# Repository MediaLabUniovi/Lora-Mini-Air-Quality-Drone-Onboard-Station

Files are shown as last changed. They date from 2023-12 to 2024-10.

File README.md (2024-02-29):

<div align="right">

spanish | english

</div>



<div align="center">

# MINI ESTACIÓN DE CALIDAD DEL AIRE CONECTADA POR LORA A BORDO DE UN DRONE

 [![Build with PlatformIO](https://img.shields.io/badge/build%20with-PlatformIO-orange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)](https://platformio.org/)

## Proyecto basado en: [alexcorvis84/mini-lora-weatherstation](https://github.com/alexcorvis84/mini-lora-weatherstation)

</div>

___

<div align="justify">

## Índice
- [Introducción](https://github.com/medialablpwan/droneloraminiairqualitystation/blob/main/README.md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)
- [Características principales](https://github.com/medialablpwan/droneloraminiairqualitystation/blob/main/README.md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)
- [Lista de componentes](https://github.com/medialablpwan/droneloraminiairqualitystation/blob/main/README.md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)
- [Lista de conexiones](https://github.com/medialablpwan/droneloraminiairqualitystation/blob/main/README.md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)
- [Flujograma (¡Simplificado!)](https://github.com/medialablpwan/droneloraminiairqualitystation/blob/main/README.md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)
- [Archivos de código](https://github.com/medialablpwan/droneloraminiairqualitystation/blob/main/README.md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)
- [Ejemplos consultados](https://github.com/medialablpwan/loraminiairqualitydroneonboardstation/blob/main/README.md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)
- [Experimento de implementación](https://github.com/medialablpwan/droneloraminiairqualitystation/blob/main/README.md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)
- [Licencia](https://github.com/medialablpwan/droneloraminiairqualitystation/blob/main/README.md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)
- [Contacto](https://github.com/medialablpwan/droneloraminiairqualitystation/blob/main/README.md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)

</div>

___

<div align="justify">

## Introducción [:leftwards_arrow_with_hook:](https://github.com/medialablpwan/droneloraminiairqualitystation/blob/main/README.md#%C3%ADndice)

Como parte de mi Trabajo de Fin de Grado sobre drones y sensorización, en Medialab_ LPWAN, se me dio a conocer la tecnología de LoRaWAN. Con ella, entendí rápidamente el potencial de trabajar en un sensor de calidad de aire que montar en un drone de _long range_ para ser usado como plataforma móvil y medir a kilómetros de distancia atmósferas hostiles en caso de accidente donde fuese peligroso enviar a un equipo de personas. Como resultado, nació el sensor _on-board_ que os voy a mostrar como un nodo conectado por LoRa, sincronizable con [The Things Network](https://www.thethingsnetwork.org/), que montarle al drone que construí sin que la cobertura fuese un factor limitante.

</div>

<div align="center">
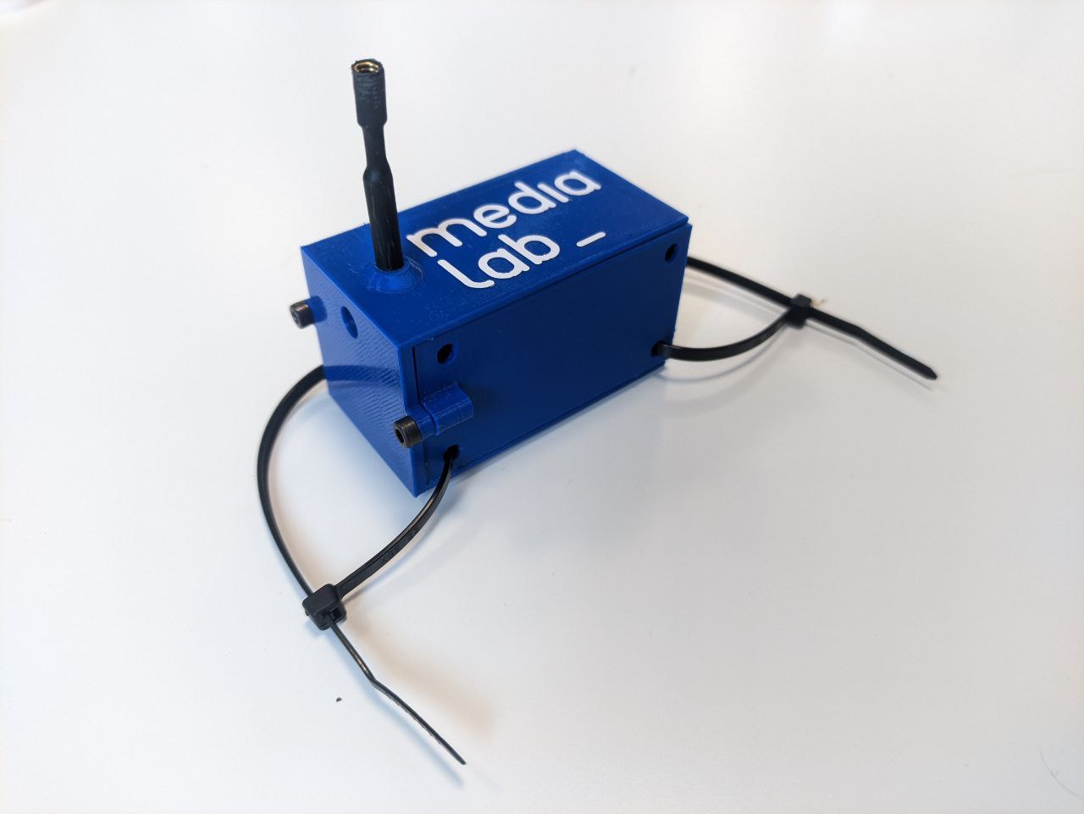
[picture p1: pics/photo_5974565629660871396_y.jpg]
  
</div>
<br/>

<p align="justify"> En este repositorio, encontrarás todos los archivos y guías educativas necesarias para entender con totalidad e incluso tomarte la libertad creativa de mejorar este proyecto. Las carpetas y archivos han sido llamados con nombres que se explican a ellos mismos para hacer la navegación más intuitiva. </p>

___

### <p align="justify"> Características principales [:leftwards_arrow_with_hook:](https://github.com/medialablpwan/droneloraminiairqualitystation/blob/main/README.md#%C3%ADndice) </p>

- <p align="justify"> Desarrollado usando la HelTec CubeCell HTCC-AB01 (Una placa de muy bajo consumo con LoRa implementado y que soporta recarga con panel solar y gestión de batería) </p>

  <div align="center">
    
  </div>
  <br/>

- <p align="justify"> Cambios realizados para añadirle, además, un sensor CCS811 (Sensor de partículas volátiles) </p>

  <div align="center">
    
  </div>
  <br/>

- <p align="justify"> Carcasa a medida para encapsular todos los componentes a un tamaño similar al de la batería del drone (Envase + Recipiente) </p>

  <div align="center">
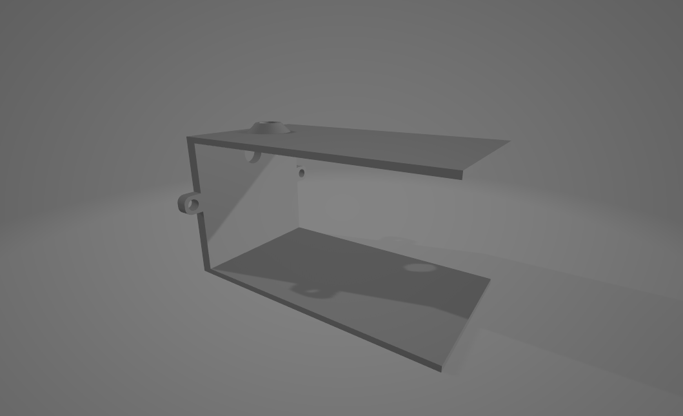
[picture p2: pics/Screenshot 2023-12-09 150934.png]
    
  </div>
  <br/>
  <div align="center">
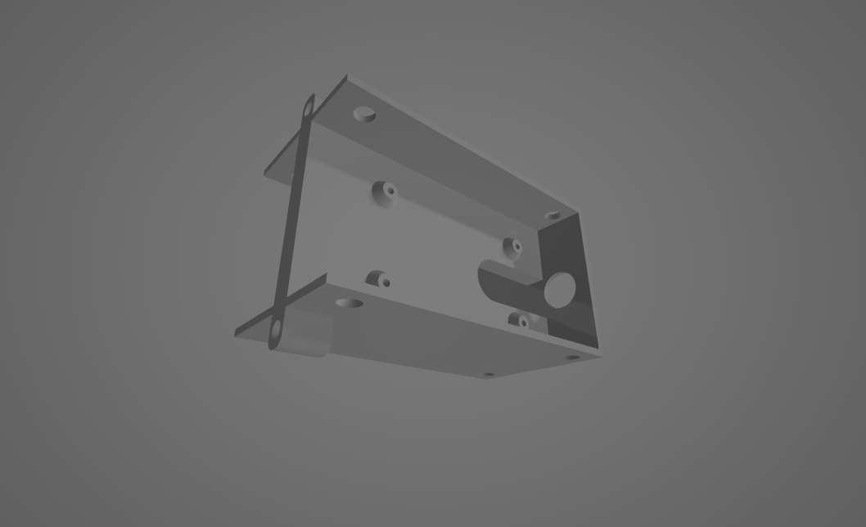
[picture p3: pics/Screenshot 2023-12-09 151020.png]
    
  </div>
  <br/>

  > Ejemplo de ensamblaje:
  <div align="center">
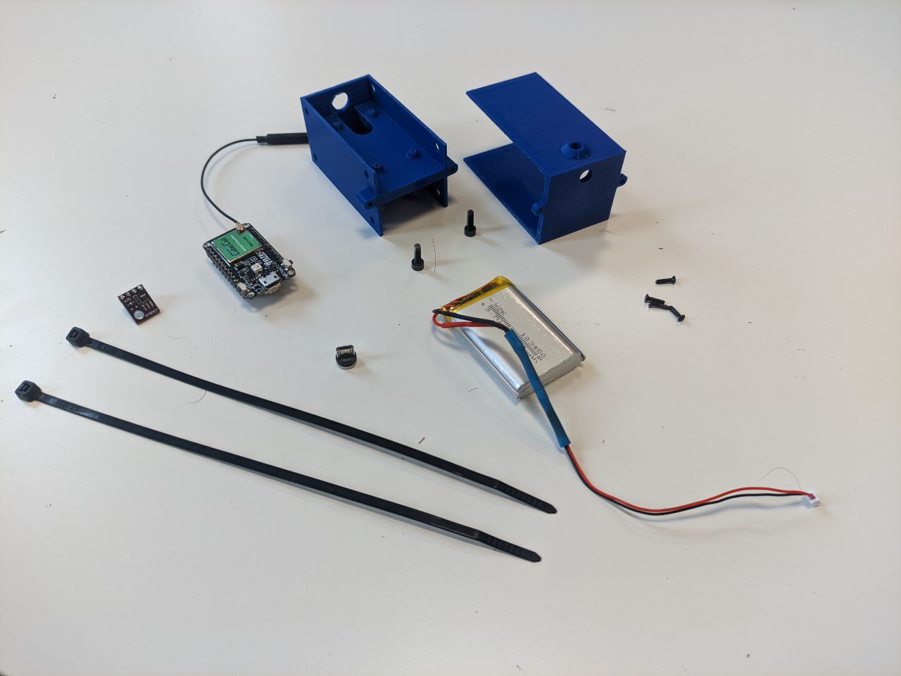
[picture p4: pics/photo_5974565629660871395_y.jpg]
    
  </div>
  <br/>

> [!WARNING]
> Hacen falta seis tornillos M3 para fijar el ensamblado y dos bridas para ajustarlo al frame del drone

___

### <p align="justify"> Lista de componentes [:leftwards_arrow_with_hook:](https://github.com/medialablpwan/droneloraminiairqualitystation/blob/main/README.md#%C3%ADndice) </p>

<div align="center">

| Componente | Modelo |
| --- | --- |
| Placa  | [CubeCell HTCC-AB01](https://es.aliexpress.com/item/1005005164213870.html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) |
| Sensor atmosférico  | [BME280](https://www.amazon.es/AZDelivery-GY-BME280-Sensor-Parent/dp/B082KL18WW) |
| Sensor de partículas volátiles  | [CCS811](https://www.amazon.es/detecci%C3%B3n-di%C3%B3xido-carbono-Detecci%C3%B3n-CJMCU-811/dp/B0CM34TX8W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) |
| Batería | [LiPo 1S 300mAh](https://www.amazon.es/EEMB-Bater%C3%ADa-pol%C3%ADmero-Recargable-Conector/dp/B09DPPP8ZV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) |
| Carcasa  | [A medida (archivo inlcuido)](https://github.com/medialablpwan/droneloraminiairqualitystation/tree/main/carc) |

</div>

___

### <p align="justify"> Lista de conexiones [:leftwards_arrow_with_hook:](https://github.com/medialablpwan/droneloraminiairqualitystation/blob/main/README.md#%C3%ADndice) </p>

<div align="center">

| BME280 | CCS811 | LiPo | CubeCell |
| --- | --- | --- | --- |
| `SDA` | `SDA` | - | `SDA` |
| `SCL` | `SCL` | - | `SCL` |
| `VIN` | - | - | `VEXT` |
| `GND` | `GND` | - | `GND` |
| - | `VCC` | - | `VDD` |
| - | `WAK` | - | `GPIO0` |
| - | - | `Con Bat` | `Con Bat` |

</div>

> En una protoboard se ve de la siguienta forma:

<div align="center">
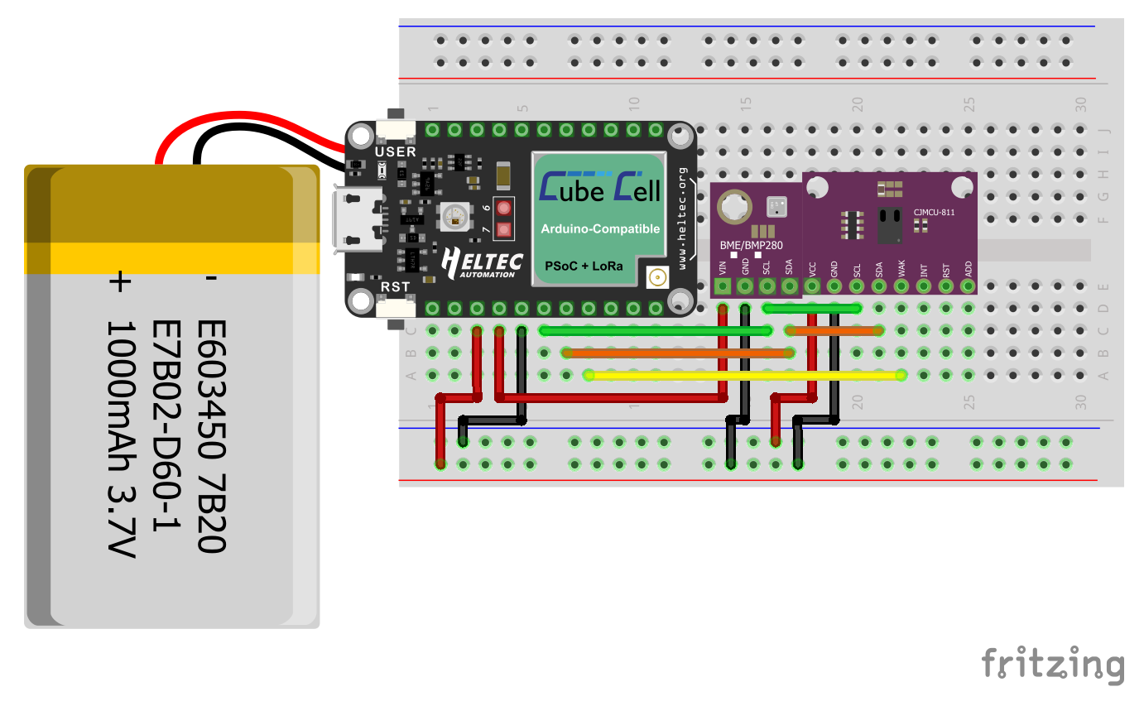
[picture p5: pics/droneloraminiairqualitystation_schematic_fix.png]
  
</div>
<br/>

> [!NOTE]
> Teniendo en cuenta que el programa hace uso del deep sleep de la CubeCell, el sensor BME280 se pone en sleep entre mensajes gracias a que el pin `VEXT` se puede gobernar (_HIGH/LOW_), mientras que el CCS811, por su uso de agentes químicos para obtener las medidas, se conecta al pin `VDD` _estático_ (incluso en deep sleep aporta corriente), y es el pin `GPIO0`,conectado al pin `WAK` del sensor, el que emite una señal digital (_HIGH/LOW_) el que lo echa a sleep

___

### <p align="justify"> Flujograma (¡Simplificado!) [:leftwards_arrow_with_hook:](https://github.com/medialablpwan/droneloraminiairqualitystation/blob/main/README.md#%C3%ADndice) </p>

```mermaid
graph TD;
  A[Encender] -->|1| B(Conectarse a una red LoRaWAN)
  B -->|2| C(Obtener las medidas de la batería y de los sensores BME y CCS)
  C -->|3| D(Mandar los bytes a TTN)
  D -->|4| E(Temporizar la tasa de transmisión de datos)
  E -->|5| F(Ir a deep sleep)
  F -->|6| B
```

___

<div align="justify">

### Archivos de código [:leftwards_arrow_with_hook:](https://github.com/medialablpwan/droneloraminiairqualitystation/blob/main/README.md#%C3%ADndice)

En esta sección, se da una descripción breve a cómo está distribuido el código entre los archivos en [`medialablpwan/droneloraminiairqualitystation/main/src/`](https://github.com/medialablpwan/droneloraminiairqualitystation/tree/main/src), donde el código está disponible para flashear o editar:

- [`main.cpp`](https://github.com/medialablpwan/droneloraminiairqualitystation/blob/main/src/main.cpp)
  ```C
  /*
  Algoritmo completo
  */
  ```
- [`credentials.h`](https://github.com/medialablpwan/lorawaterlevelmonitoring/blob/main/main/credentials.h)
  ```C
  /*
  Claves OTAA para sincronizarse en TTN
  */
  ```

Un análisis más en profundidad viene dado en el propio código ya que cada función está explicada con comentarios.

</div>

___

<div align="justify">

### Ejemplos consultados [:leftwards_arrow_with_hook:](https://github.com/medialablpwan/droneloraminiairqualitystation/blob/main/README.md#%C3%ADndice)

En esta sección se listan los ejemplos de código oficiales de HelTec usados para adaptar el proyecto original a los objetivos de éste y si han sido finalmente útiles:

- [x] [LoRaWAN _¡Hola, Mundo!_](https://github.com/HelTecAutomation/CubeCell-Arduino/blob/master/libraries/LoRa/examples/LoRaWAN/LoRaWan/LoRaWan.ino)

- [ ] [LoRaWAN CCS811](https://github.com/HelTecAutomation/CubeCell-Arduino/blob/master/libraries/LoRa/examples/LoRaWAN/LoRaWAN_Sensors/LoRaWan_CCS811/LoRaWan_CCS811.ino)

- [x] [LoRaWAN multisensor](https://github.com/HelTecAutomation/CubeCell-Arduino/blob/master/libraries/LoRa/examples/LoRaWAN/LoRaWAN_Sensors/LoRaWan_MultiSensor/include/prepareTxFrame.cpp)

- [ ] [LoRaWAN BMP280](https://github.com/HelTecAutomation/CubeCell-Arduino/blob/master/libraries/LoRa/examples/LoRaWAN/LoRaWAN_Sensors_ThirdParty/examples/LoRaWAN_BMP280/LoRaWAN_BMP280.in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)

- [x] [CCS811 Test (CCS811.h)](https://github.com/HelTecAutomation/CubeCell-Arduino/blob/master/libraries/SensorBasic/examples/CCS811/CCS811_test/CCS811_test.ino)

- [ ] [CCS Example (Adafruit_CCS811.h)](https://github.com/HelTecAutomation/CubeCell-Arduino/blob/master/libraries/Sensor_ThirdParty/examples/CCS811/CCS811_test/CCS811_test.ino)

- [x] [BME280 Example](https://github.com/HelTecAutomation/CubeCell-Arduino/blob/master/libraries/Sensor_ThirdParty/examples/BME280/bme280_example/bme280_example.ino)

</div>

___

___

## <p align="justify"> Experimento de implementación [:leftwards_arrow_with_hook:](https://github.com/medialablpwan/droneloraminiairqualitystation/blob/main/README.md#%C3%ADndice) </p>

### <p align="justify"> El ensamblaje final ha quedado de la siguiente manera: </p>

<div align="center">
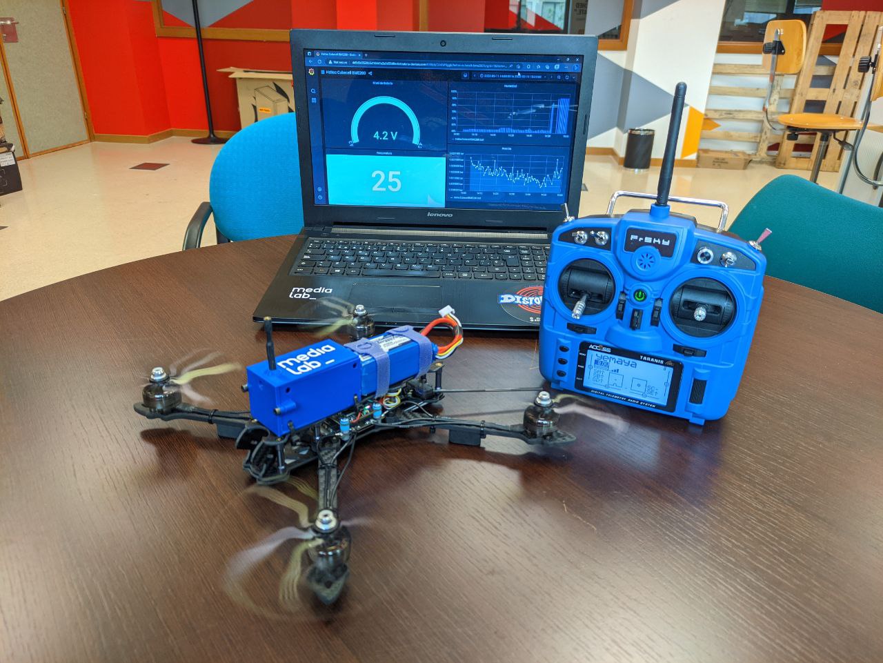
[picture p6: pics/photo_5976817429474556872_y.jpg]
  
</div>
<br/>

___

### Accede al panel de Grafana[^1] por medio de este código QR o el link de debajo:

<div align="center">
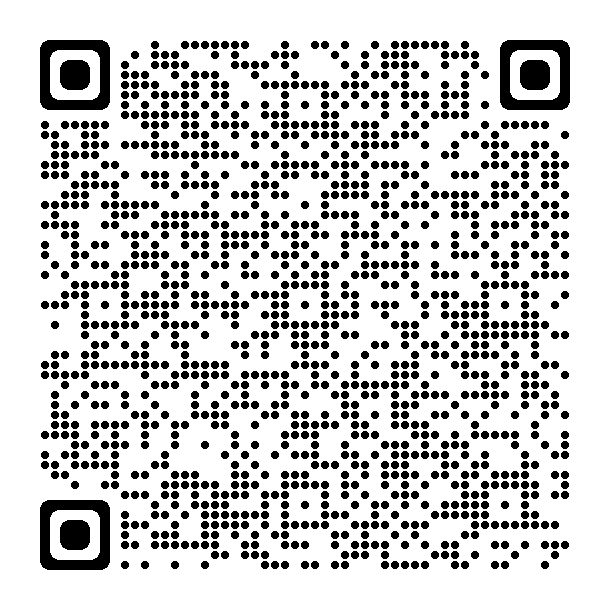
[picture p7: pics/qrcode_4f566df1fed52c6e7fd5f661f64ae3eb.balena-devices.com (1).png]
  
</div>
<br/>

<p align="center"> http://4f566df1fed52c6e7fd5f661f64ae3eb.balena-devices.com:8080/d/1bwgnfzgk/heltec-cubecell-bme280-ccs811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 </p>

___

___

## <p align="justify"> Licencia [:leftwards_arrow_with_hook:](https://github.com/medialablpwan/droneloraminiairqualitystation/blob/main/README.md#%C3%ADndice) </p>

Este proyecto está licenciado bajo la [GPL-3.0 license](https://github.com/medialablpwan/droneloraminiairqualitystation/blob/main/LICENSE). Contiene código de [alexcorvis84/mini-lora-weatherstation](https://github.com/alexcorvis84/mini-lora-weatherstation)

___

### <p align="justify"> Contacto [:leftwards_arrow_with_hook:](https://github.com/medialablpwan/droneloraminiairqualitystation/blob/main/README.md#%C3%ADndice) </p>

> [!IMPORTANT]
> Responderemos amablemente a dudas y leeremos sugerencias: 
> 
> Más información sobre nuestras actividades: 

_<p align="justify"> Autores: Daniel Rodríguez Moya, Iván Graña y el grupo de trabajo de MediaLab\_ LPWAN :shipit: </p>_

[^1]: Instrucciones sobre como desplegar paneles de Grafana en el siguiente repo [`medialablpwan/documentacion`](https://github.com/medialablpwan/documentacion).

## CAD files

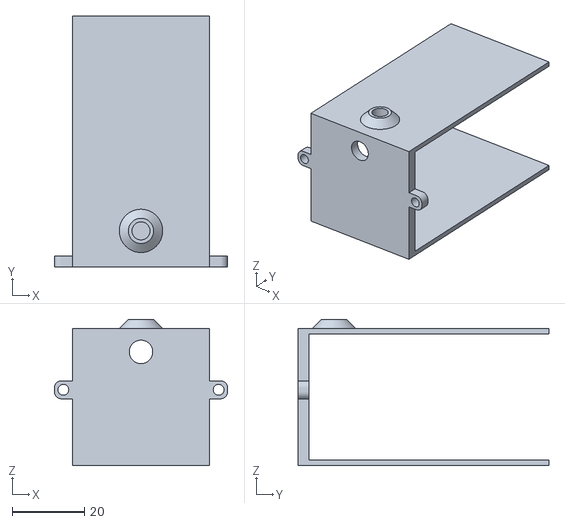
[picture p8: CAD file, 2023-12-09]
3d-printed-parts/Tapa Cube Cell IV.stl
48.0 x 69.5 x 40.5

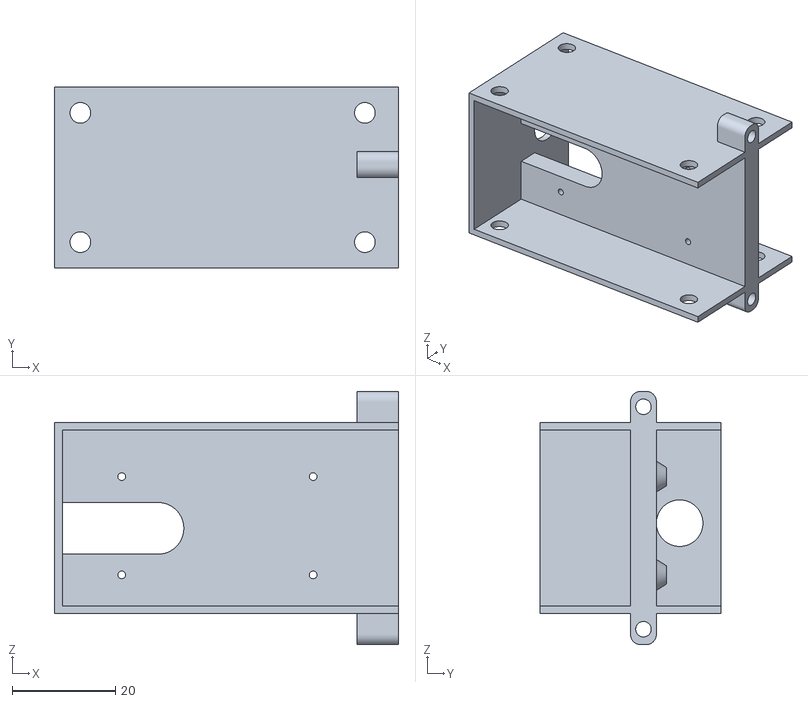
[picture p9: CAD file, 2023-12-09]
3d-printed-parts/Base Cueb Cell IV.stl
66.5 x 35.0 x 49.0

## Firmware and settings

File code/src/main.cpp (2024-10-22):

/* ***********************************************************************************************************
SENSOR ALI V1.2 - MEDIALAB LPWAN UNIVERSIDAD DE OVIEDO

Este archivo ha sido modificado de manera considerable para implementar el sensor de CO2 y particulas
volatiles, además del original BME280. El enlace para consultar el proyecto original del usuario de GitHub
"alexcorvis84" es el siguiente: https://github.com/alexcorvis84/mini-lora-weatherstation.git
*********************************************************************************************************** */

// 'includes' for libraries and header files -----------------------------------------------------------------
#include <LoRaWan_APP.h>                                                    // HelTec LoRa library
#include <Arduino.h>
#include <Seeed_BME280.h>
#include <CCS811.h>                                                         // HelTec modified version of Adafruit_CCS811 library (inlcuded in HelTec documentation)
#include <Wire.h>
#include "credentials.h"                                                    // OTAA keys to synchronize with TTN

// 'defines' for various aims --------------------------------------------------------------------------------
#define ENABLE_DEBUG 1                                                      // Toggle to enable/disable serial monitor
                                                
// LoRaWAN technic declarations -----------------------------------------------------------------------------
uint32_t appTxDutyCycle = 90000;                                            // Data transmission rate time (in milliseconds). Cannot be declared and initialized in other ways as it refers to a library variable
uint16_t userChannelsMask[6]={ 0x00FF,0x0000,0x0000,0x0000,0x0000,0x0000 };
LoRaMacRegion_t loraWanRegion = ACTIVE_REGION;                              // Macro that represents the region, EU868
DeviceClass_t  loraWanClass = LORAWAN_CLASS;                                // Macro that represents the device class, A
bool overTheAirActivation = LORAWAN_NETMODE;                                // Macro that represents the type of LoRa activation, OTAA
bool loraWanAdr = LORAWAN_ADR;                                              // LoRa address
bool keepNet = LORAWAN_NET_RESERVE;
bool isTxConfirmed = LORAWAN_UPLINKMODE;                                    // TX needs to be confirmed
uint8_t appPort = 2;
uint8_t confirmedNbTrials = 4;                                              // Trials of TX

// Sensors variables -----------------------------------------------------------------------------------------
int temperature, batteryVoltage;
uint8_t humidity;
long pressure;
uint16_t co2_medida, tvoc_medida;

// Sensors constructors -------------------------------------------------------------------------------------
BME280 bme;
CCS811 ccs;

// Function to get the average measurement of CO2 and TVOC out of 5 individual measurements -----------------
void ccs_medida(){
  co2_medida = 0;
  tvoc_medida = 0;
  if(!ccs.readData()){                                                      // 'ccs.readData()' is kinda tricky. It returns a true if no measurements are available, and false if it successfully found something to show. That is why it partnered with a not (!)
    co2_medida = ccs.geteCO2();                                             // Both 'ccs.getCO2()' and 'ccs.getTVOC()' return the values
    tvoc_medida = ccs.getTVOC();                                            // TVOC: Total Volatile Organic Compounds
    Serial.print("El CO2 es: ");
    Serial.println(co2_medida);
    Serial.print("El TVOC es: ");
    Serial.println(tvoc_medida);
  }
  else{
    Serial.println("ERROR!");
  }
}

// Function to prepare the transmission =====================================================================
static void prepareTxFrame(uint8_t port){
  pinMode(Vext, OUTPUT);                                                    // Vext is a reserved word to refer to the 3.3V pin of the CubeCell board, it enables the output to power the sensor
  digitalWrite(Vext, LOW);                                                  // SET IT TO LOW MEANS ENABLING 3.3V, IT WORKS "INVERSELY"
	
  pinMode(GPIO0, OUTPUT);                                                   // GPIO0 is used to control the 'WAK' pin of the CCS, enabling and disabling sleep mode of the sensor
	digitalWrite(GPIO0, LOW);                                                 // It is set to LOW when reading as "GND" makes it be awake. Kinda contra-intuitive, I know
	
  pinMode(GPIO4, OUTPUT);                                                   // RGB LED GPIO
	digitalWrite(GPIO4, HIGH);

  delay(500);                                                               // Small courtesy delay for pin modes

  Serial.println("Sensor Ali v1.2 test");

  Wire.begin();                                                             // Initialization of I2C communication

  delay(100);                                                               // Small courtesy delay for I2C communication

  // If BME does not init, print error if serial enabled ----------------------------------------------------
  if(!bme.init()){
    Serial.println("Could not find a valid BME280 sensor, check wiring!");
  }

  delay(500);                                                               // This delay is required to allow the sensor time to init

  // Initialization of the variables to the BME library functions -------------------------------------------
  temperature = bme.getTemperature() * 100;                                 // As temperature is give with two decimals, it is converted to 'int'
  humidity = bme.getHumidity();
  pressure = bme.getPressure();                                             // Pressure in Pa

  delay(100);                                                               // Delay between sensors

  // If CCS does not begin, print an error if serial enabled ------------------------------------------------
  if(!ccs.begin()){
    Serial.println("Failed to start sensor! Please check your wiring.");
    while(1);
  }

  delay(500);                                                               // This delay is required to allow the sensor time to init

  while(!ccs.available());                                                  // Wait for the sensor to be ready

  delay(5000);                                                              // This delay is required to allow the sensor time to be available

  ccs_medida();

  Wire.end();                                                               // End of I2C communication
  
  // Turn the power to the sensor off again ----------------------------------------------------------------
  digitalWrite(Vext, HIGH);                                                 // SET IT TO HIGH, DISABLING 3.3V OUTPUT, REMEMBER IS CONTRA-INTUITIVE
	digitalWrite(GPIO0, HIGH);                                                // CCS 'WAK' pin control to HIGH as this enables the sleep mode
	digitalWrite(GPIO4, LOW);

  batteryVoltage = getBatteryVoltage();                                     // Built-in function to get battery voltage

  // TX bytes array initialization --------------------------------------------------------------------------
  appDataSize = 13;
  appData[0] = lowByte(temperature);                                        // As temperature values range from bigger than 256 (more than a byte) and less than 65536 (less than 2 bytes), functions 'lowByte' and 'highByte' are needed
  appData[1] = highByte(temperature);

  appData[2] = lowByte(humidity);

  appData[3] = (byte) ((pressure & 0xFF000000) >> 24 );
  appData[4] = (byte) ((pressure & 0x00FF0000) >> 16 );
  appData[5] = (byte) ((pressure & 0x0000FF00) >> 8  );
  appData[6] = (byte) ((pressure & 0X000000FF)       );

  appData[7] = highByte(batteryVoltage);
  appData[8] = lowByte(batteryVoltage);

  appData[9] = lowByte(co2_medida);
  appData[10] = highByte(co2_medida);

  appData[11] = lowByte(tvoc_medida);
  appData[12] = highByte(tvoc_medida);

  // Serial monitor messages to debug -----------------------------------------------------------------------
  Serial.print("Temperature: ");
  Serial.print(temperature / 100);
  Serial.print("C, Humidity: ");
  Serial.print(humidity);
  Serial.print("%, Pressure: ");
  Serial.print(pressure);
  Serial.print(" hPa, Battery Voltage: ");
  Serial.print(batteryVoltage);
  Serial.println(" V");

  Serial.print("CO2: ");
  Serial.print(co2_medida);
  Serial.print("ppm, TVOC: ");
  Serial.println(tvoc_medida);
}

// 'setup()' function =======================================================================================
void setup(){
  // ONLY the initialization of the CubeCell board ----------------------------------------------------------
  boardInitMcu();
  if(ENABLE_DEBUG == 1){
    Serial.begin(115200);                                                   // It is here where serial is initialized
  }

  deviceState = DEVICE_STATE_INIT;                                          // State that indicates the process of joining a LoRaWAN network
  LoRaWAN.ifskipjoin();
}

// 'loop()' function ========================================================================================
void loop(){
  // CubeCell LoRaWAN state machine -------------------------------------------------------------------------
  switch(deviceState){

    // State that indicates the process of joining a LoRaWAN network ----------------------------------------
    case DEVICE_STATE_INIT:
    {
      printDevParam();
      LoRaWAN.init(loraWanClass,loraWanRegion);
      deviceState = DEVICE_STATE_JOIN;                                      // Following state is the one that indicates the process of actively joined the network
      break;
    }

    // State that indicates the process of having joined a LoRaWAN network -----------------------------------
    case DEVICE_STATE_JOIN:
    {
      LoRaWAN.join();                                                       // Function to join the network
      break;
    }

    // Automatically change to send state --------------------------------------------------------------------
    case DEVICE_STATE_SEND:
    {
      prepareTxFrame(appPort);
      LoRaWAN.send();                                                       // Function so send the bytes
      deviceState = DEVICE_STATE_CYCLE;                                     // Following state is the one to time the data transmission rate
      break;
    }

    // State that indicates the process of timing the data transmission rate --------------------------------
    case DEVICE_STATE_CYCLE:
    {
      txDutyCycleTime = appTxDutyCycle + randr(0, APP_TX_DUTYCYCLE_RND);    // Schedule next packet transmission. 'APP_TX_DUTYCYCLE_RND' defines a random delay for application data transmission duty cycle. 1s
      LoRaWAN.cycle(txDutyCycleTime);
      deviceState = DEVICE_STATE_SLEEP;                                     // Following state is to activate deep sleep
      break;
    }

    // State that indicates the process of starting deep sleep between cycles -------------------------------
    case DEVICE_STATE_SLEEP:
    {
      LoRaWAN.sleep();                                                      // Function to activate deep sleep for the timed time
      break;
    }

    default:
    {
      deviceState = DEVICE_STATE_INIT;
      break;
    }
  }
}

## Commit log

2023-12-14 fixed bad wire connection between CubeCell and CCS
2023-12-14 fixed wrong pin connection between CubeCell and CCS
2024-10-22 update directories
    [Base Cueb Cell IV.stl, Tapa Cube Cell IV.stl]
